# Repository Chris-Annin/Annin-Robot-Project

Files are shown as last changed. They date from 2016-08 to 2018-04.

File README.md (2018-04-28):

# Annin Robot Project

## 6 axis stepper motor robot and control software

This project includes:

- Bill of materials and instructions
- CAD files to 3D print components to build the robot
- Arduino sketch for stepper driver control
- Software to program and operate robot

All geared stepper motors and drivers are available from  [www.omc-stepperonline.com](https://www.omc-stepperonline.com/?tracking=59c1139e8987b)
all other misc hardware are off the shelf items available from multiple sources (see the bill of materials file)

(https://www.youtube.com/watch?v=XkAfb8alqnI)

This was my first Arduino program and my first python application using the Tk module.
I hope people will enjoy building thier own robot, utilize and improve the software
and design and build bigger and better robot units and share thier designs.

1. review the bill of materials
2. review the assembly instructions
3. download models and build robot
4. review calibration video [Calibration Video](https://youtu.be/jC1Iq60EnBI)
5. review programming video [Programming Video](https://youtu.be/hFJe0j0nB_w)

please view license file

Questions: chris.annin@gmail.com
#


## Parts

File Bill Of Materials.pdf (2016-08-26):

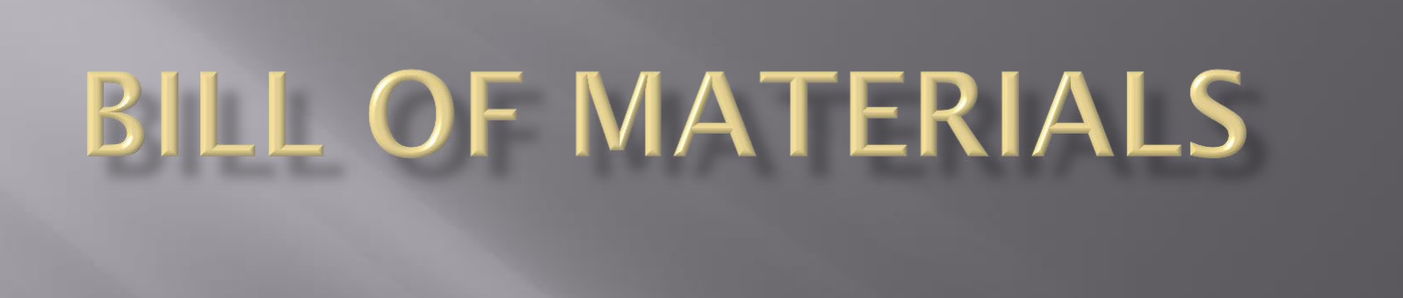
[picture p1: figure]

## This BOM includes all the major parts to build the robot. These parts were purchased from Amazon, McMaster Carr, Ebay, the local hardware store and also parts you need to print on your 3D

printer. There are a few misc. screws and wires I may have missed.

## If there is not a note below the picture stating quantity then just buy

one of the item shown.

# Amazon parts – these are in no particular order

You need a total of 3 of these bearings so I
Bought 2 (2 packs) | You need a total of 4 of these bearings

You need a total of 2 of these thrust bearings

I bought 2 of these 5vdc power supplies One to power the stepper drivers and one To power my relays

There is a cheaper power supply on Amazon that would probably work fine It needs to be 24vdc and 10 to 15 amp

You do not need the power supply – just the Breadboard and wires (power supply is garbage)

1 stepper motor for axis 5 1 stepper motor for axis 4

You need 2 of these needle bearings | 1 stepper motor for axis 6
For axis 4

You need 2 of these stepper motors for axis 1 and 2 1 stepper motors for axis 3

You need a total of 6 stepper drivers – so you Will need to purchase 2 (5 packs)

## This tubing was purchased From McMaster Carr

## This gear was from Ebay

## Parts purchased from local hardware store

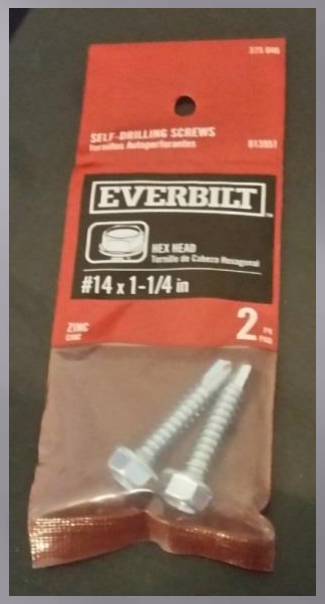
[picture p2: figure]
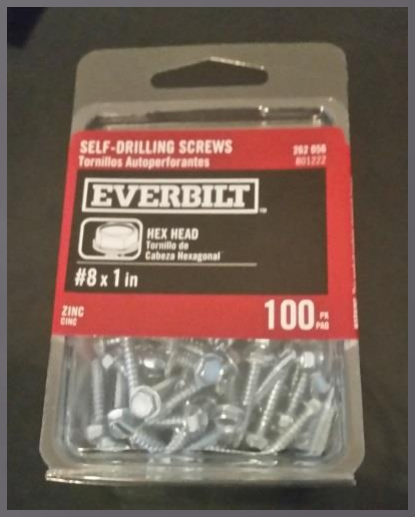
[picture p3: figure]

NEED 4 #14 SCREWS TO MOUNT BASE

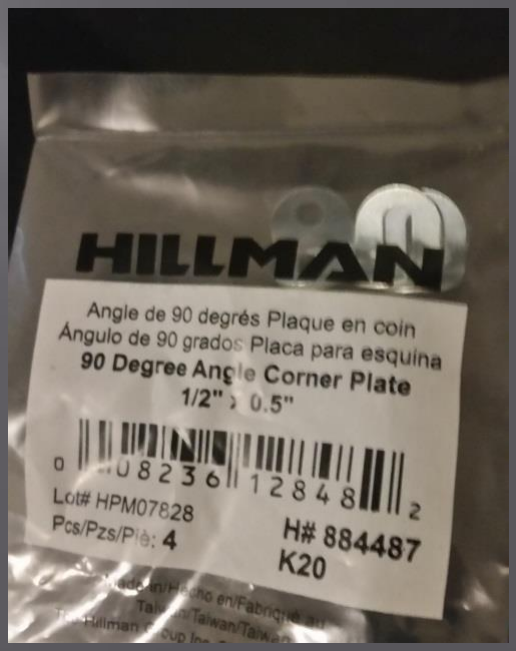
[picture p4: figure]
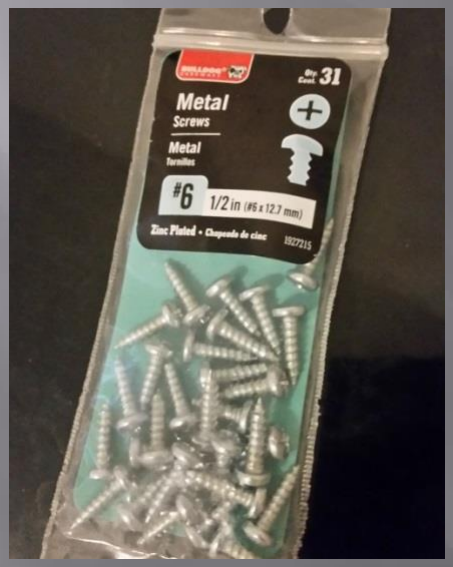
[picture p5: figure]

NEED #6 SCREW ½” AND 3/8” LONG

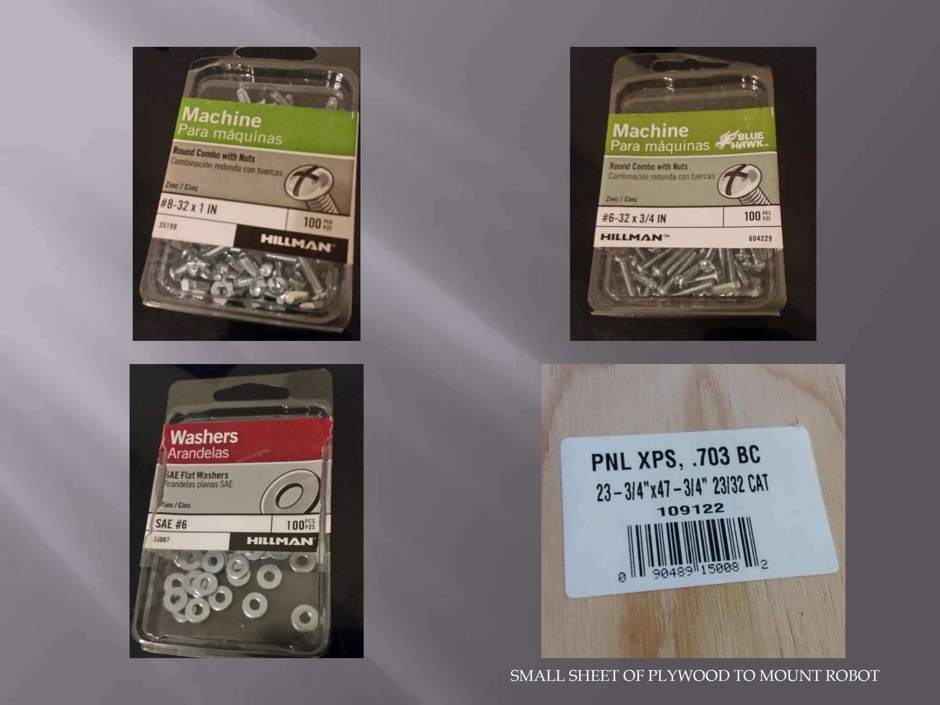
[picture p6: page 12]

SMALL SHEET OF PLYWOOD TO MOUNT ROBOT

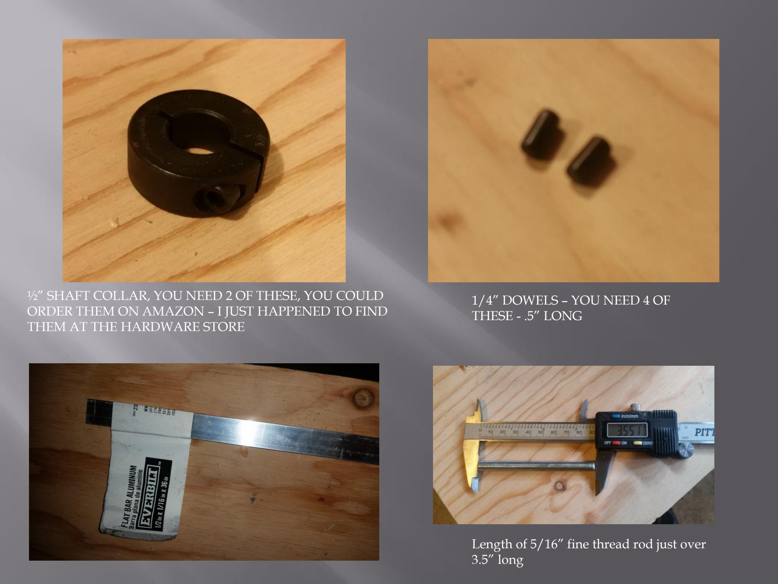
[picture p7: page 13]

½” SHAFT COLLAR, YOU NEED 2 OF THESE, YOU COULD ORDER THEM ON AMAZON – I JUST HAPPENED TO FIND THEM AT THE HARDWARE STORE

1/4” DOWELS – YOU NEED 4 OF THESE - .5” LONG

Length of 5/16” fine thread rod just over 3.5” long

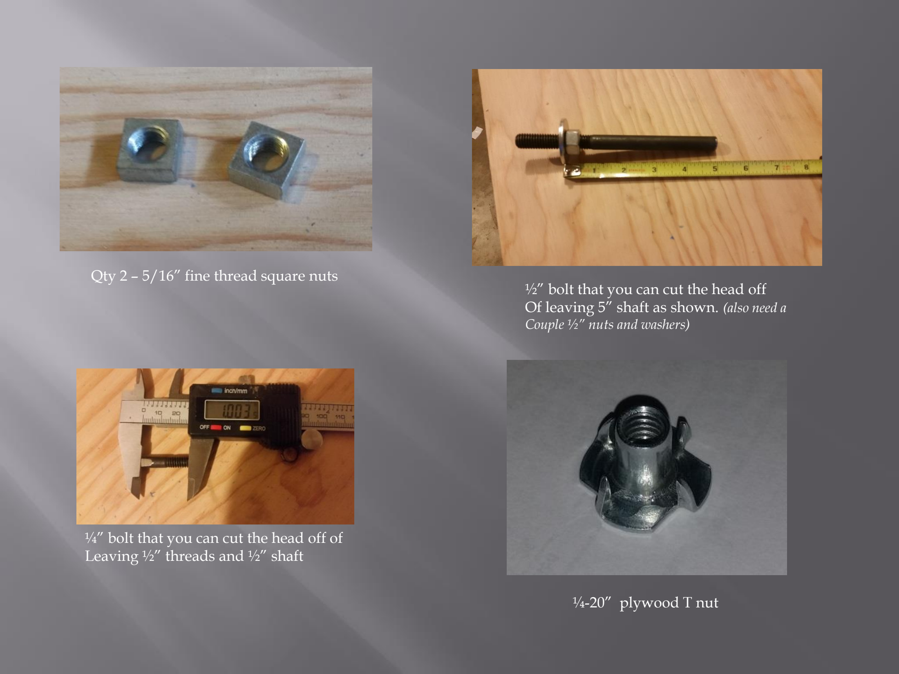
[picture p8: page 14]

Qty 2 – 5/16” fine thread square nuts ½” bolt that you can cut the head off Of leaving 5” shaft as shown. (also need a Couple ½” nuts and washers)

¼” bolt that you can cut the head off of Leaving ½” threads and ½” shaft

¼-20” plywood T nut

ADDITIONALLY YOU WILL NEED A NUMBER OF METRIC MACHINE SCREWS, 2mm & 3mm. I was able to find what I needed at the hardware store but you can also get screw assortments on Amazon.


¼-20” bolt that you can cut The head off leaving total 1” long With .5” threads and .5” shaft.


2” long coil springs – I got these out
Of a harbor freight spring assortment I had.

## Parts you need to print on your 3D printer

(I printed all these on a Davinci XYZ 1.0 - unless otherwise noted these were all printed at 50% solid, thick shells, 2mm layers, slow speed with no supports)

J1 Base | J1 Alignment Ring
J1 Turret | J1 Turret Cover

I didn’t have good luck using supports for these larger thin wall holes So I built the model with cut outs you will need to grind out with a dremel

J2 Arm Left
J2 Arm Right

J2 Spacers

J2 Motor Support

Used supports on this one

J2 Drive Rod Support Block J2 Drive Block

J2 Arm Cover (x2)
J3 Turret

Used supports on this one
Used supports on this one

Used supports on this one

J3 Spindle

Collar 1 inch

J3 Turret Cap | J4 Boom – Left & Right (left not pictured)
Used supports on this one | Used supports on this one

J5 Motor Mount

J5 Clevis Center | J5 Clevis Left Arm & Right Arm
J5 Turret Left and Right Arms / J5 Turret Center | Gear J5 Ring Carrier / Gear J5 Ring Carrier Cap Gear J5 Worm Bushing

Timing Belt Coupler
J4 Wire Holder (x2)

Gripper Motor Side Plate
Gripper Cover Side Plate Printed 90% solid on this one – wanted area where J6 motor

Shaft inserts to be solid

Gripper Center Spur Gear
Gripper Right Jaw
Gripper Left Jaw | Home Cradle

Printed 90% solid on this one Printed 90% solid on this one

Printed 90% solid on this one | Printed 30% solid on this one – this part doesn’t need much strength And is too large to print with much mass

Relay Board Mount

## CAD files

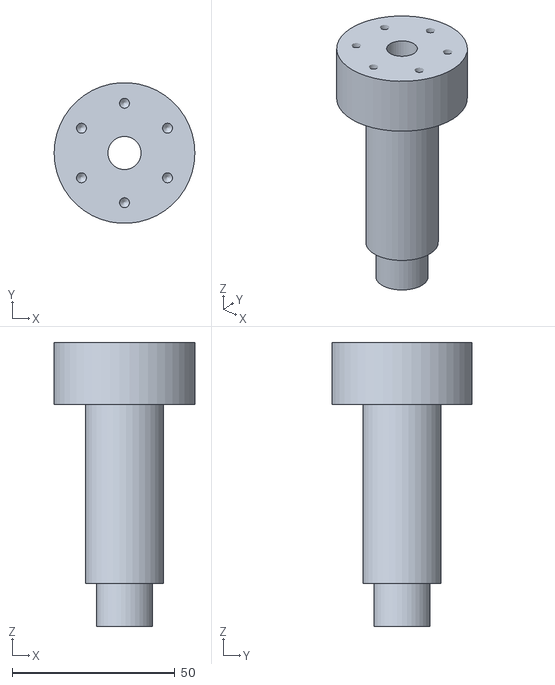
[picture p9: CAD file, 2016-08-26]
STL files/J3 Spindle.STL
43.2 x 43.1 x 87.1

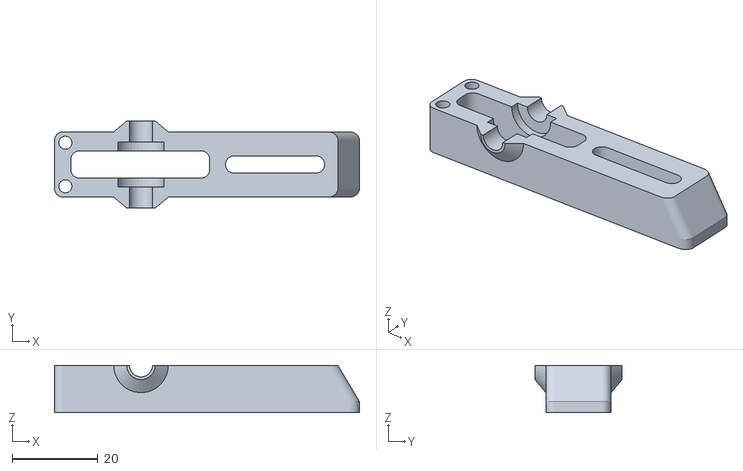
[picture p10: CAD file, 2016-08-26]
STL files/Gear J5 ring carrier.STL
71.1 x 20.3 x 11.0

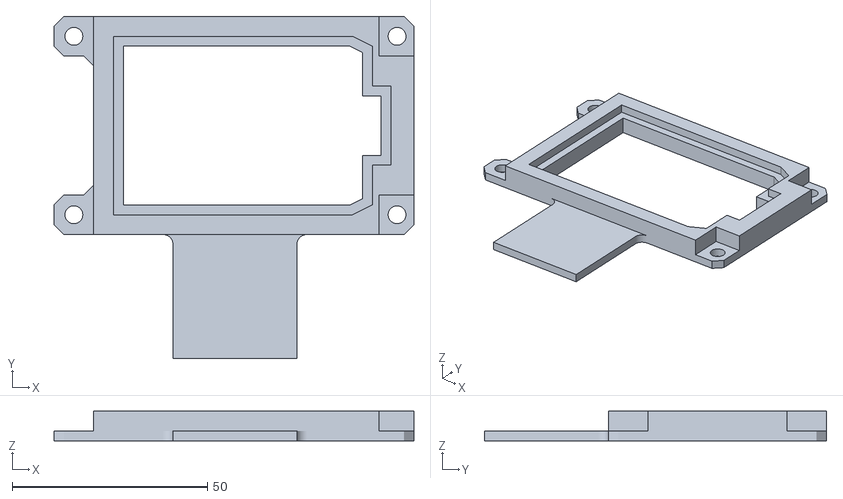
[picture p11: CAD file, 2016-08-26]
STL files/Mouse Holder.STL
92.2 x 87.6 x 7.62

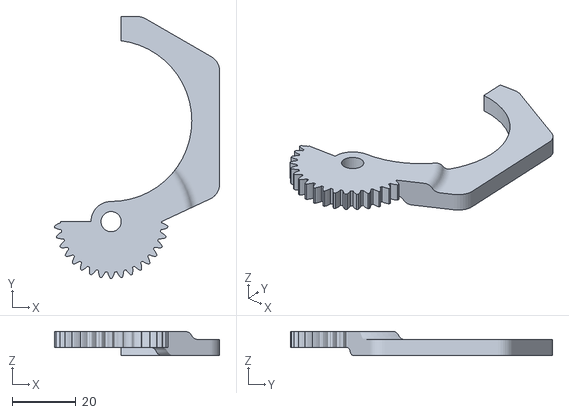
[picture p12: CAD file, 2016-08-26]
STL files/Gripper left jaw.STL
52.0 x 82.5 x 7.62

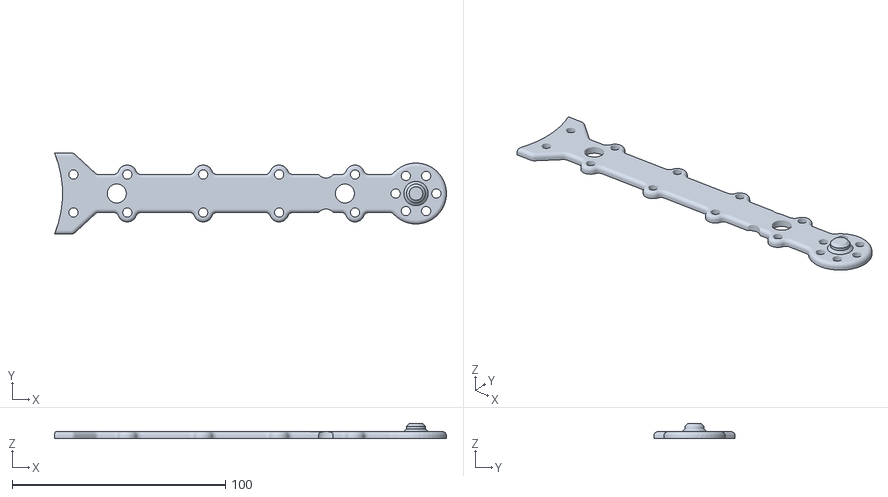
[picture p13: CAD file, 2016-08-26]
STL files/J2 Arm Cover.STL
183.6 x 38.0 x 6.98

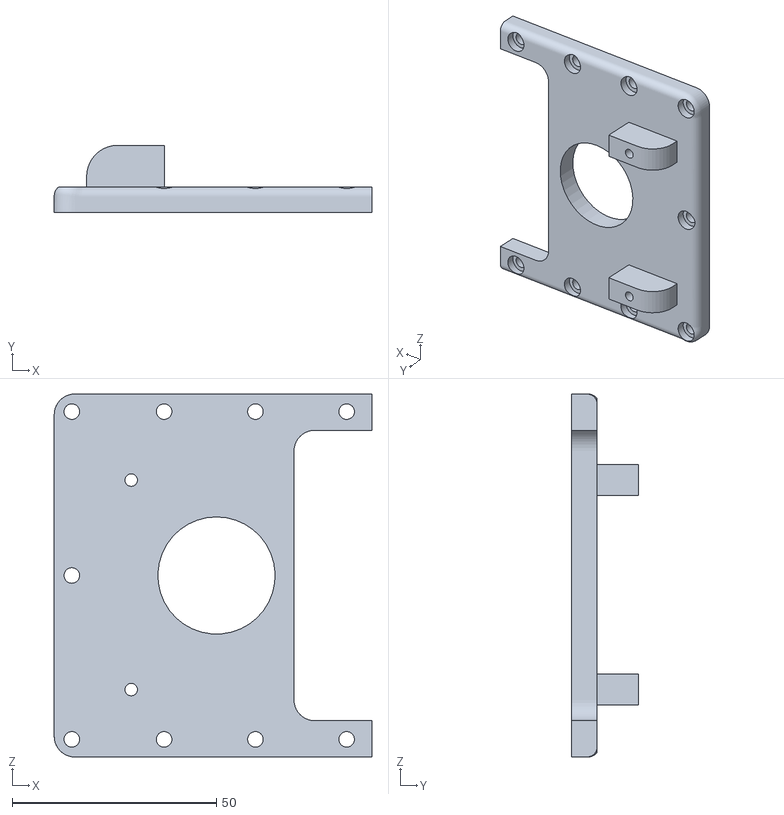
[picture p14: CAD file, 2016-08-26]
STL files/J1 Turret cover.STL
77.8 x 16.5 x 88.9

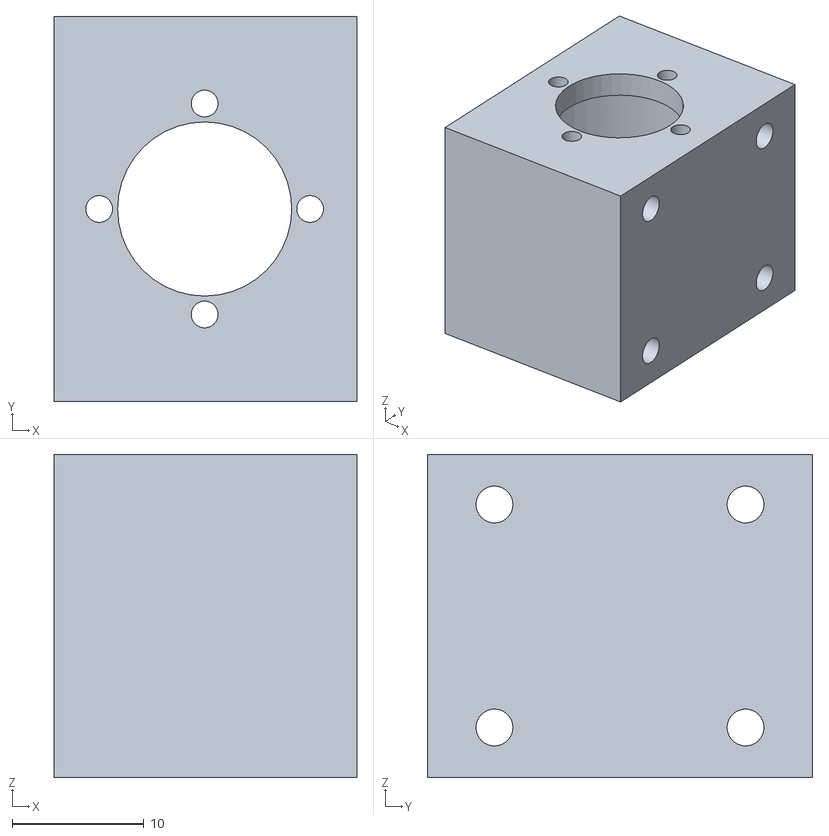
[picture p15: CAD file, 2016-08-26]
STL files/J5 Turret Center.STL
23.0 x 29.2 x 24.5

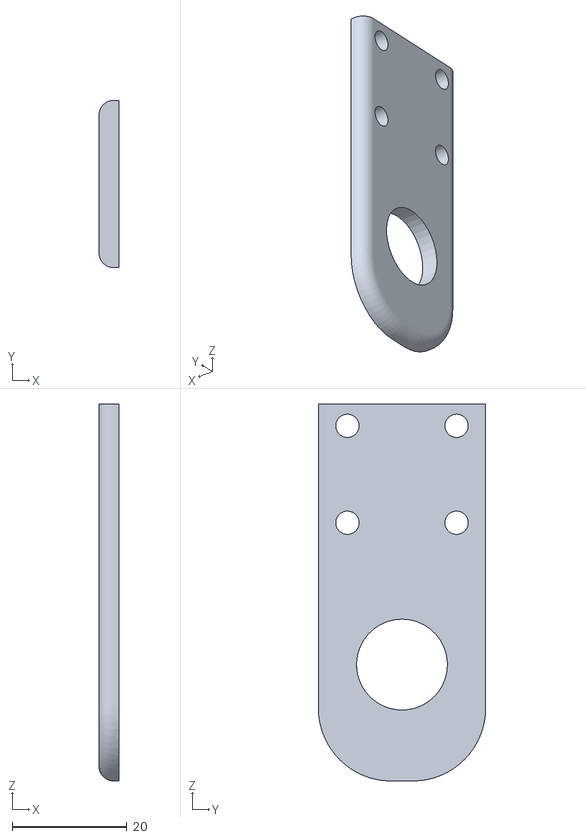
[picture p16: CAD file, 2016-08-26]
STL files/J5 Turret Right Arm.STL
3.49 x 29.2 x 65.8

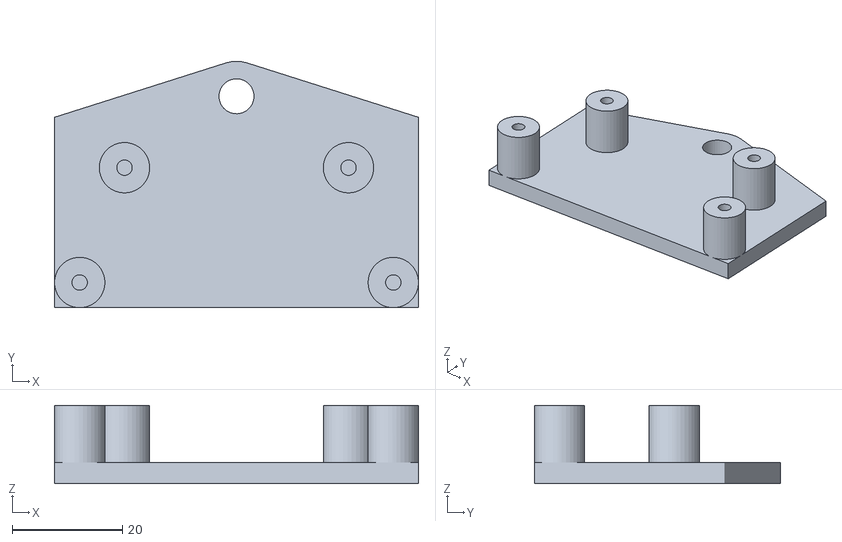
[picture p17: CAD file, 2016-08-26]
STL files/Gripper Cover side plate.STL
66.0 x 44.7 x 14.2

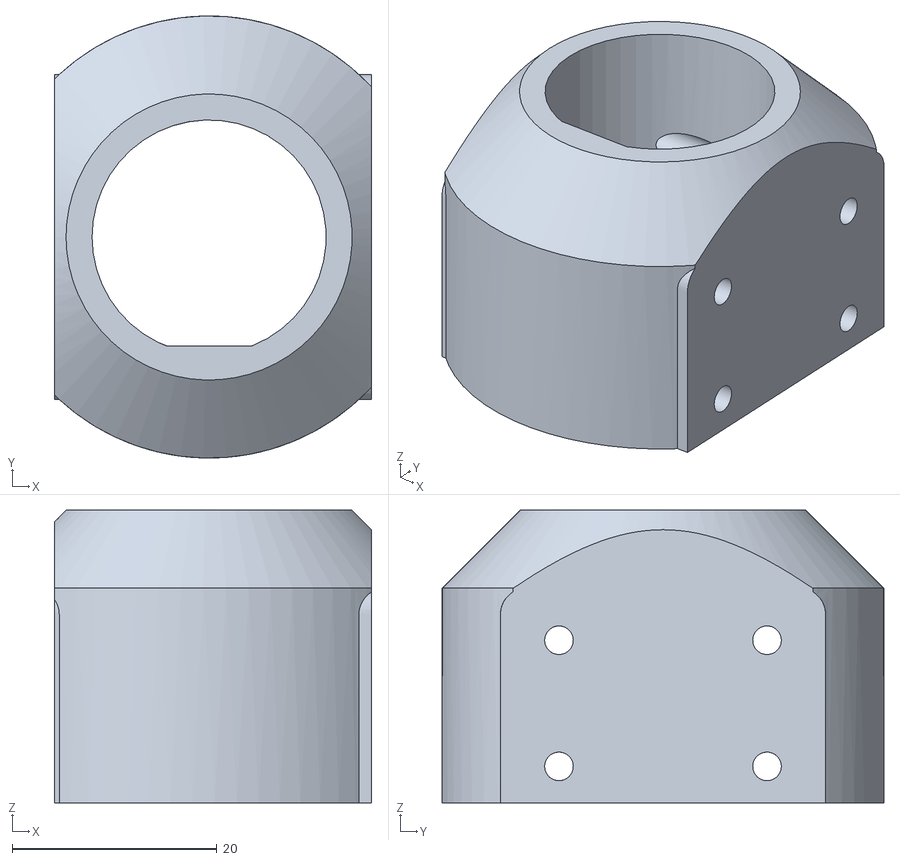
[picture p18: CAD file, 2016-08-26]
STL files/J5 Clevis Center.STL
31.0 x 43.2 x 28.6

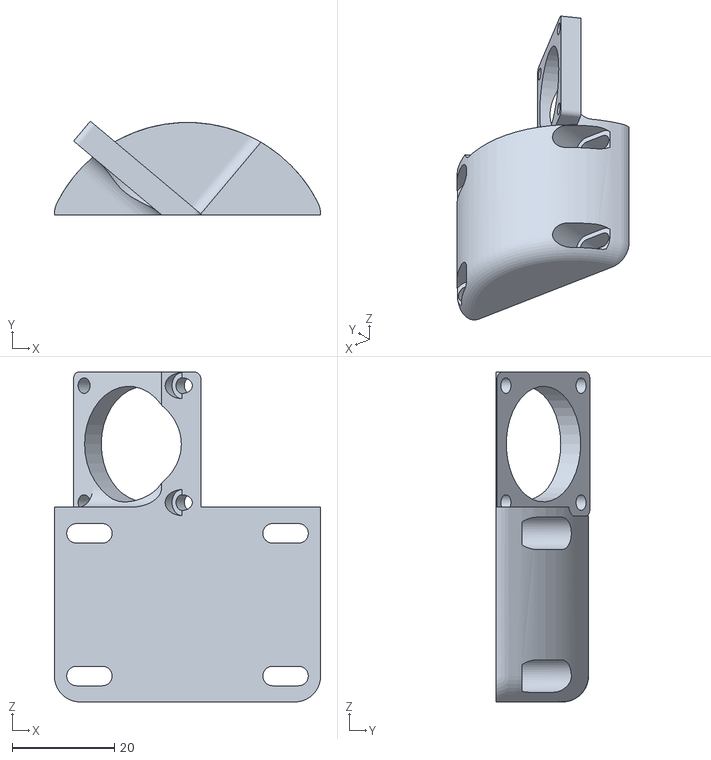
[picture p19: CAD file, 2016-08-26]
STL files/J3 Turret cap.STL
52.1 x 18.3 x 64.5

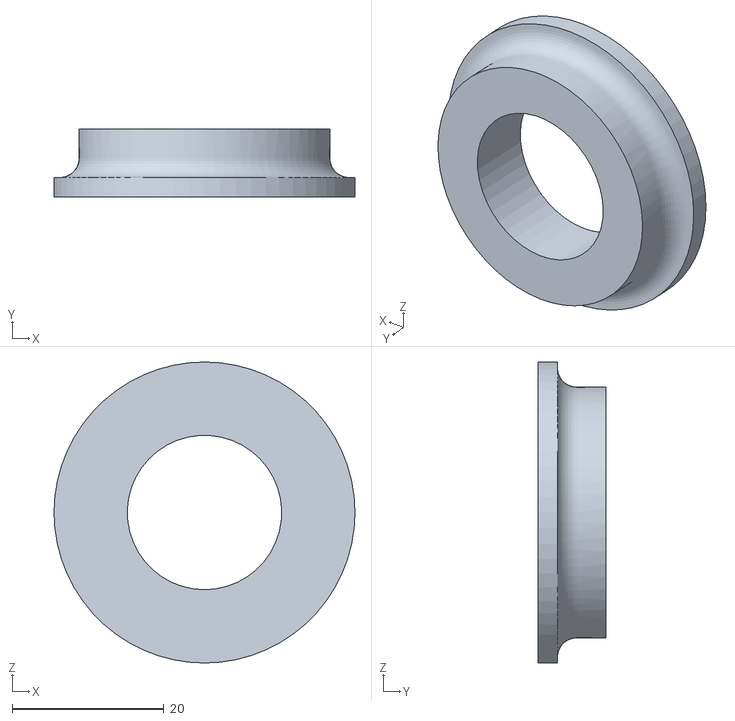
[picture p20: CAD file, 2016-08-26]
STL files/Collar 1 inch.STL
39.6 x 8.89 x 39.6

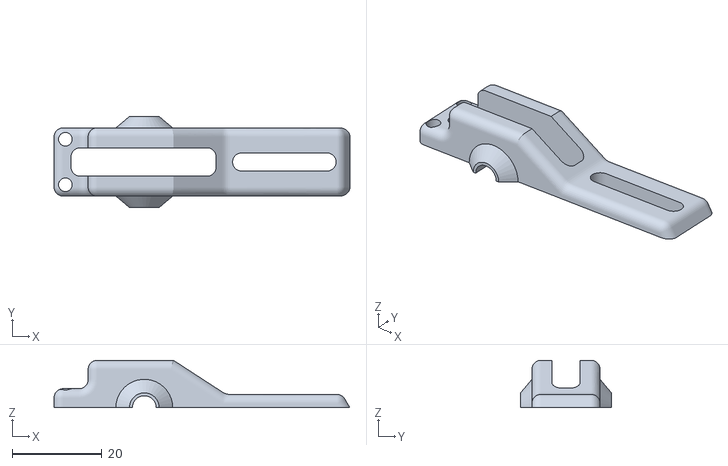
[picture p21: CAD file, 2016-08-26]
STL files/Gear J5 ring carrier cap.STL
66.1 x 20.3 x 10.6

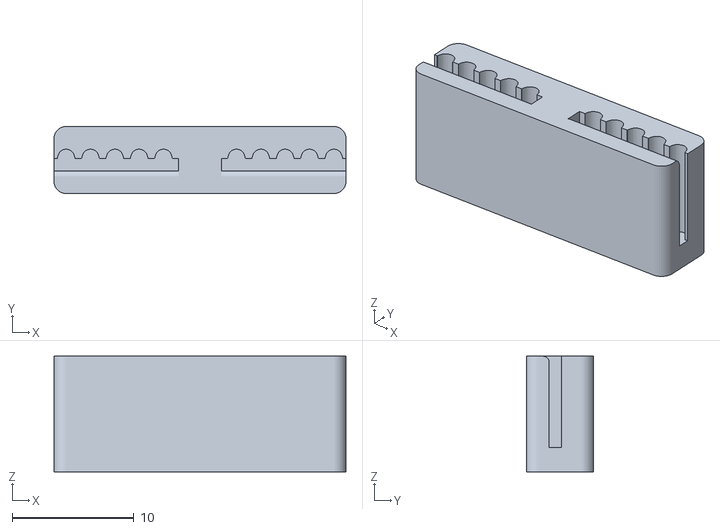
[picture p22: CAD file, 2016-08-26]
STL files/timing belt coupler.STL
24.0 x 5.52 x 9.50

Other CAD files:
STL files/Gripper right jaw.STL
STL files/J2 Spacer 2.STL
STL files/J2 Motor Support.STL
STL files/J2 Drive Rod Support Block.STL
STL files/Arduino Mount.STL
STL files/Gear J5 worm bushing.STL
STL files/Gripper Motor side plate.STL
STL files/Gripper center spur.STL
STL files/Home cradle.STL
STL files/J1 Alignment Ring.STL
STL files/J1 Base.STL
STL files/J1 Turret.STL
STL files/J2 Arm Left.STL
STL files/J2 Arm Right.STL
STL files/J2 Drive Block.STL
STL files/J2 Spacer.STL
STL files/J2 nut cap.STL
STL files/J3 Turret.STL
STL files/J4 Boom left.STL
STL files/J4 Boom right.STL
STL files/J4 Boom.STL
STL files/J4 Collar 1 inch.STL
STL files/J4 wire holder.STL
STL files/J5 Clevis Left Arm.STL
STL files/J5 Clevis Right Arm.STL
STL files/J5 Clevis.STL
STL files/J5 Motor Mount.STL
STL files/J5 Turret Left Arm.STL
STL files/J5 Turret.STL
STL files/coupler.STL

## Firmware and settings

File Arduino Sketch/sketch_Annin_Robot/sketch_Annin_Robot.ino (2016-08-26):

/* Annin Robot - Stepper motor robot control software
    Copyright (C) 2016  Chris Annin

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
    chris.annin@gmail.com
*/    

#include <Servo.h>

Servo servo0;
Servo servo1;
Servo servo2;
Servo servo3;
Servo servo4;
Servo servo5;
Servo servo6;
Servo servo7;

String inData;
String function;

const int J1stepPin = 2;
const int J1dirPin = 3;
const int J2stepPin = 4;
const int J2dirPin = 5;
const int J3stepPin = 6;
const int J3dirPin = 7;
const int J4stepPin = 8;
const int J4dirPin = 9;
const int J5stepPin = 10;
const int J5dirPin = 11;
const int J6stepPin = 12;
const int J6dirPin = 13;

const int Input22 = 22;
const int Input23 = 23;
const int Input24 = 24;
const int Input25 = 25;
const int Input26 = 26;
const int Input27 = 27;
const int Input28 = 28;
const int Input29 = 29;
const int Input30 = 30;
const int Input31 = 31;
const int Input32 = 32;
const int Input33 = 33;
const int Input34 = 34;
const int Input35 = 35;
const int Input36 = 36;
const int Input37 = 37;

const int Output38 = 38;
const int Output39 = 39;
const int Output40 = 40;
const int Output41 = 41;
const int Output42 = 42;
const int Output43 = 43;
const int Output44 = 44;
const int Output45 = 45;
const int Output46 = 46;
const int Output47 = 47;
const int Output48 = 48;
const int Output49 = 49;
const int Output50 = 50;
const int Output51 = 51;
const int Output52 = 52;
const int Output53 = 53;


void setup() {
  // put your setup code here, to run once:
  Serial.begin(9600);

  pinMode(A0, OUTPUT);
  pinMode(A1, OUTPUT);
  pinMode(A2, OUTPUT);
  pinMode(A3, OUTPUT);
  pinMode(A4, OUTPUT);
  pinMode(A5, OUTPUT);
  pinMode(A6, OUTPUT);
  pinMode(A7, OUTPUT);

  pinMode(J1stepPin, OUTPUT);
  pinMode(J1dirPin, OUTPUT);
  pinMode(J2stepPin, OUTPUT);
  pinMode(J2dirPin, OUTPUT);
  pinMode(J3stepPin, OUTPUT);
  pinMode(J3dirPin, OUTPUT);
  pinMode(J4stepPin, OUTPUT);
  pinMode(J4dirPin, OUTPUT);
  pinMode(J5stepPin, OUTPUT);
  pinMode(J5dirPin, OUTPUT);
  pinMode(J6stepPin, OUTPUT);
  pinMode(J6dirPin, OUTPUT);

  pinMode(Input22, INPUT);
  pinMode(Input23, INPUT);
  pinMode(Input24, INPUT);
  pinMode(Input25, INPUT);
  pinMode(Input26, INPUT);
  pinMode(Input27, INPUT);
  pinMode(Input28, INPUT);
  pinMode(Input29, INPUT);
  pinMode(Input30, INPUT);
  pinMode(Input31, INPUT);
  pinMode(Input32, INPUT);
  pinMode(Input33, INPUT);
  pinMode(Input34, INPUT);
  pinMode(Input35, INPUT);
  pinMode(Input36, INPUT);
  pinMode(Input37, INPUT);

  pinMode(Output38, OUTPUT);
  pinMode(Output39, OUTPUT);
  pinMode(Output40, OUTPUT);
  pinMode(Output41, OUTPUT);
  pinMode(Output42, OUTPUT);
  pinMode(Output43, OUTPUT);
  pinMode(Output44, OUTPUT);
  pinMode(Output45, OUTPUT);
  pinMode(Output46, OUTPUT);
  pinMode(Output47, OUTPUT);
  pinMode(Output48, OUTPUT);
  pinMode(Output49, OUTPUT);
  pinMode(Output50, OUTPUT);
  pinMode(Output51, OUTPUT);
  pinMode(Output52, OUTPUT);
  pinMode(Output53, OUTPUT);

  servo0.attach(A0);
  servo1.attach(A1);
  servo2.attach(A2);
  servo3.attach(A3);
  servo4.attach(A4);
  servo5.attach(A5);
  servo6.attach(A6);
  servo7.attach(A7);

  digitalWrite(Output38, HIGH);
  digitalWrite(Output39, HIGH);
  digitalWrite(Output40, HIGH);
  digitalWrite(Output41, HIGH);
  digitalWrite(Output42, HIGH);
  digitalWrite(Output43, HIGH);
  digitalWrite(Output44, HIGH);
  digitalWrite(Output45, HIGH);

}


void loop() {
  while (Serial.available() > 0)
  {
    char recieved = Serial.read();
    inData += recieved;
    // Process message when new line character is recieved
    if (recieved == '\n')
    {
      String function = inData.substring(0, 2);


      //-----COMMAND TO MOVE SERVO---------------------------------------------------
      //-----------------------------------------------------------------------
      if (function == "SV")
      {
        int SVstart = inData.indexOf('V');
        int POSstart = inData.indexOf('P');
        int servoNum = inData.substring(SVstart + 1, POSstart).toInt();
        int servoPOS = inData.substring(POSstart + 1).toInt();
        if (servoNum == 0)
        {
          servo0.write(servoPOS);
        }
        if (servoNum == 1)
        {
          servo1.write(servoPOS);
        }
        if (servoNum == 2)
        {
          servo2.write(servoPOS);
        }
        if (servoNum == 3)
        {
          servo3.write(servoPOS);
        }
        if (servoNum == 4)
        {
          servo4.write(servoPOS);
        }
        if (servoNum == 5)
        {
          servo5.write(servoPOS);
        }
        if (servoNum == 6)
        {
          servo6.write(servoPOS);
        }
        if (servoNum == 7)
        {
          servo7.write(servoPOS);
        }
        Serial.print("Servo Done");
      }




      //-----COMMAND TO WAIT TIME---------------------------------------------------
      //-----------------------------------------------------------------------
      if (function == "WT")
      {
        int WTstart = inData.indexOf('S');
        float WaitTime = inData.substring(WTstart + 1).toFloat();
        int WaitTimeMS = WaitTime * 1000;
        delay(WaitTimeMS);
        Serial.print("Done");
      }

      //-----COMMAND IF INPUT THEN JUMP---------------------------------------------------
      //-----------------------------------------------------------------------
      if (function == "IJ")
      {
        int IJstart = inData.indexOf('X');
        int IJTabstart = inData.indexOf('T');
        int IJInputNum = inData.substring(IJstart + 1, IJTabstart).toInt();
        if (digitalRead(IJInputNum) == HIGH)
        {
          Serial.println("True\n");
        }
        if (digitalRead(IJInputNum) == LOW)
        {
          Serial.println("False\n");
        }
      }
      //-----COMMAND SET OUTPUT ON---------------------------------------------------
      //-----------------------------------------------------------------------
      if (function == "ON")
      {
        int ONstart = inData.indexOf('X');
        int outputNum = inData.substring(ONstart + 1).toInt();
        digitalWrite(outputNum, HIGH);
        Serial.print("Done");
      }
      //-----COMMAND SET OUTPUT OFF---------------------------------------------------
      //-----------------------------------------------------------------------
      if (function == "OF")
      {
        int ONstart = inData.indexOf('X');
        int outputNum = inData.substring(ONstart + 1).toInt();
        digitalWrite(outputNum, LOW);
        Serial.print("Done");
      }
      //-----COMMAND TO WAIT INPUT ON---------------------------------------------------
      //-----------------------------------------------------------------------
      if (function == "WI")
      {
        int WIstart = inData.indexOf('N');
        int InputNum = inData.substring(WIstart + 1).toInt();
        while (digitalRead(InputNum) == LOW) {
          delay(100);
        }
        Serial.print("Done");
      }
      //-----COMMAND TO WAIT INPUT OFF---------------------------------------------------
      //-----------------------------------------------------------------------
      if (function == "WO")
      {
        int WIstart = inData.indexOf('N');
        int InputNum = inData.substring(WIstart + 1).toInt();

        //String InputStr =  String("Input" + InputNum);
        //uint8_t Input = atoi(InputStr.c_str ());
        while (digitalRead(InputNum) == HIGH) {
          delay(100);
        }
        Serial.print("Done");
      }
      //-----COMMAND TO MOVE---------------------------------------------------
      //-----------------------------------------------------------------------
      if (function == "MJ")
      {
        int J1start = inData.indexOf('A');
        int J2start = inData.indexOf('B');
        int J3start = inData.indexOf('C');
        int J4start = inData.indexOf('D');
        int J5start = inData.indexOf('E');
        int J6start = inData.indexOf('F');
        int SPstart = inData.indexOf('S');
        int J1dir = inData.substring(J1start + 1, J1start + 2).toInt();
        int J2dir = inData.substring(J2start + 1, J2start + 2).toInt();
        int J3dir = inData.substring(J3start + 1, J3start + 2).toInt();
        int J4dir = inData.substring(J4start + 1, J4start + 2).toInt();
        int J5dir = inData.substring(J5start + 1, J5start + 2).toInt();
        int J6dir = inData.substring(J6start + 1, J6start + 2).toInt();
        int J1step = inData.substring(J1start + 2, J2start).toInt();
        int J2step = inData.substring(J2start + 2, J3start).toInt();
        int J3step = inData.substring(J3start + 2, J4start).toInt();
        int J4step = inData.substring(J4start + 2, J5start).toInt();
        int J5step = inData.substring(J5start + 2, J6start).toInt();
        int J6step = inData.substring(J6start + 2, SPstart).toInt();
        float SpeedIn = inData.substring(SPstart + 1).toFloat();
        SpeedIn = (SpeedIn / 100);
        float CalcSpeed = (1600 / SpeedIn);
        int Speed = int(CalcSpeed);

        //FIND HIGHEST STEP
        int highStep = J1step;
        if (J2step > highStep)
        {
          highStep = J2step;
        }
        if (J3step > highStep)
        {
          highStep = J3step;
        }
        if (J4step > highStep)
        {
          highStep = J4step;
        }
        if (J5step > highStep)
        {
          highStep = J5step;
        }
        if (J6step > highStep)
        {
          highStep = J6step;
        }



        //DETERMINE AXIS SKIP INCREMENT
        int J1skip = (highStep / J1step);
        int J2skip = (highStep / J2step);
        int J3skip = (highStep / J3step);
        int J4skip = (highStep / J4step);
        int J5skip = (highStep / J5step);
        int J6skip = (highStep / J6step);


        //RESET COUNTERS
        int J1done = 0;
        int J2done = 0;
        int J3done = 0;
        int J4done = 0;
        int J5done = 0;
        int J6done = 0;

        //RESET SKIP CURRENT
        int J1skipCur = 0;
        int J2skipCur = 0;
        int J3skipCur = 0;
        int J4skipCur = 0;
        int J5skipCur = 0;
        int J6skipCur = 0;

        //SET DIRECTIONS
        if (J1dir == 1)
        {
          digitalWrite(J1dirPin, HIGH);
        }
        else if (J1dir == 0)
        {
          digitalWrite(J1dirPin, LOW);
        }
        if (J2dir == 1)
        {
          digitalWrite(J2dirPin, HIGH);
        }
        else if (J2dir == 0)
        {
          digitalWrite(J2dirPin, LOW);
        }
        if (J3dir == 1)
        {
          digitalWrite(J3dirPin, HIGH);
        }
        else if (J3dir == 0)
        {
          digitalWrite(J3dirPin, LOW);
        }
        if (J4dir == 1)
        {
          digitalWrite(J4dirPin, HIGH);
        }
        else if (J4dir == 0)
        {
          digitalWrite(J4dirPin, LOW);
        }
        if (J5dir == 1)
        {
          digitalWrite(J5dirPin, HIGH);
        }
        else if (J5dir == 0)
        {
          digitalWrite(J5dirPin, LOW);
        }
        if (J6dir == 1)
        {
          digitalWrite(J6dirPin, HIGH);
        }
        else if (J6dir == 0)
        {
          digitalWrite(J6dirPin, LOW);
        }




        //DRIVE MOTORS
        while (J1done < J1step || J2done < J2step || J3done < J3step || J4done < J4step || J5done < J5step || J6done < J6step)
        {
          if (J1done < J1step && J1skipCur == 0)
          {
            digitalWrite(J1stepPin, HIGH);
          }
          if (J2done < J2step && J2skipCur == 0)
          {
            digitalWrite(J2stepPin, HIGH);
          }
          if (J3done < J3step && J3skipCur == 0)
          {
            digitalWrite(J3stepPin, HIGH);
          }
          if (J4done < J4step && J4skipCur == 0)
          {
            digitalWrite(J4stepPin, HIGH);
          }
          if (J5done < J5step && J5skipCur == 0)
          {
            digitalWrite(J5stepPin, HIGH);
          }
          if (J6done < J6step && J6skipCur == 0)
          {
            digitalWrite(J6stepPin, HIGH);
          }
          //#############DELAY AND SET LOW
          delayMicroseconds(0);
          if (J1done < J1step && J1skipCur == 0)
          {
            digitalWrite(J1stepPin, LOW);
            J1done = ++J1done;
          }
          if (J2done < J2step && J2skipCur == 0)
          {
            digitalWrite(J2stepPin, LOW);
            J2done = ++J2done;
          }
          if (J3done < J3step && J3skipCur == 0)
          {
            digitalWrite(J3stepPin, LOW);
            J3done = ++J3done;
          }
          if (J4done < J4step && J4skipCur == 0)
          {
            digitalWrite(J4stepPin, LOW);
            J4done = ++J4done;
          }
          if (J5done < J5step && J5skipCur == 0)
          {
            digitalWrite(J5stepPin, LOW);
            J5done = ++J5done;;
          }
          if (J6done < J6step && J6skipCur == 0)
          {
            digitalWrite(J6stepPin, LOW);
            J6done = ++J6done;
          }
          //#############DELAY BEFORE RESTARTING LOOP AND SETTING HIGH AGAIN
          delayMicroseconds(Speed);
          //increment skip count
          J1skipCur = ++J1skipCur;
          J2skipCur = ++J2skipCur;
          J3skipCur = ++J3skipCur;
          J4skipCur = ++J4skipCur;
          J5skipCur = ++J5skipCur;
          J6skipCur = ++J6skipCur;
          //if skiped enough times set back to zero
          if (J1skipCur == J1skip)
          {
            J1skipCur = 0;
          }
          if (J2skipCur == J2skip)
          {
            J2skipCur = 0;
          }
          if (J3skipCur == J3skip)
          {
            J3skipCur = 0;
          }
          if (J4skipCur == J4skip)
          {
            J4skipCur = 0;
          }
          if (J5skipCur == J5skip)
          {
            J5skipCur = 0;
          }
          if (J6skipCur == J6skip)
          {
            J6skipCur = 0;
          }
        }
        inData = ""; // Clear recieved buffer
        Serial.print("Move Done");
      }
      else
      {
        inData = ""; // Clear recieved buffer
      }
    }
  }
}

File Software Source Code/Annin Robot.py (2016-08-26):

##########################################################################
##########################################################################
""" Annin Robot - Stepper motor robot control software
    Copyright (C) 2016  Chris Annin

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
    chris.annin@gmail.com
"""
##########################################################################
##########################################################################


from Tkinter import *
import pickle
import serial
import time
import threading
import Queue

root = Tk()
root.wm_title("Annin Robot 1.0")
root.iconbitmap(r'ARbot.ico')
root.resizable(width=True, height=True)
root.geometry('{}x{}'.format(1024,700))
root.runTrue = 0


###DEFS###################################################################
##########################################################################


def setCom():
  global ser  
  port = "COM" + comPortEntryField.get()  
  baud = 9600 
  ser = serial.Serial(port, baud)

def deleteitem():
  selRow = root.progView.curselection()[0]
  selection = root.progView.curselection()  
  root.progView.delete(selection[0])
  root.progView.select_set(selRow)  
  value=root.progView.get(0,END)
  pickle.dump(value,open(ProgEntryField.get(),"wb"))
    

def executeRow():
  selRow = root.progView.curselection()[0]
  root.progView.see(selRow+2)
  data = map(int, root.progView.curselection())
  command=root.progView.get(data[0])
  cmdType=command[:6]
  ##Call Program##
  if (cmdType == "Call P"):
    root.lastRow = root.progView.curselection()[0]
    root.lastProg = ProgEntryField.get()
    programIndex = command.find("Program -")
    progNum = str(command[programIndex+10:])
    ProgEntryField.delete(0, 'end')
    ProgEntryField.insert(0,progNum)
    loadProg()
    time.sleep(.2)    
    index = 0
    root.progView.selection_clear(0, END)
    root.progView.select_set(index) 
  ##Return Program##
  if (cmdType == "Return"):
    lastRow = root.lastRow
    lastProg = root.lastProg
    ProgEntryField.delete(0, 'end')
    ProgEntryField.insert(0,lastProg)
    loadProg()
    time.sleep(.2)    
    index = 0
    root.progView.selection_clear(0, END)
    root.progView.select_set(lastRow)  
  ##Servo Command##
  if (cmdType == "Servo "):
    servoIndex = command.find("number ")
    posIndex = command.find("position: ")
    servoNum = str(command[servoIndex+7:posIndex-4])
    servoPos = str(command[posIndex+10:])
    command = "SV"+servoNum+"P"+servoPos
    ser.write(command +"\n")
    ser.flushInput()
    time.sleep(.1)  
    ser.read() 
  ##If Input On Jump to Tab##
  if (cmdType == "If On "):
    inputIndex = command.find("Input-")
    tabIndex = command.find("Tab-")
    inputNum = str(command[inputIndex+6:tabIndex-9])
    tabNum = str(command[tabIndex+4:])
    command = "JFX"+inputNum+"T"+tabNum   
    ser.write(command +"\n")
    ser.flushInput()
    value = ser.readline()
    #value = str(value[3:])
    manEntryField.delete(0, 'end')
    manEntryField.insert(0,value)
    if (value == "True\n"):
      index = root.progView.get(0, "end").index("Tab Number " + tabNum)
      index = index-1
      root.progView.selection_clear(0, END)
      root.progView.select_set(index)
  ##If Input Off Jump to Tab##
  if (cmdType == "If Off"):
    inputIndex = command.find("Input-")
    tabIndex = command.find("Tab-")
    inputNum = str(command[inputIndex+6:tabIndex-9])
    tabNum = str(command[tabIndex+4:])
    command = "JFX"+inputNum+"T"+tabNum   
    ser.write(command +"\n")
    ser.flushInput()
    value = ser.readline()
    #value = str(value[3:])
    manEntryField.delete(0, 'end')
    manEntryField.insert(0,value)
    if (value == "False\n"):
      index = root.progView.get(0, "end").index("Tab Number " + tabNum)
      index = index-1
      root.progView.selection_clear(0, END)
      root.progView.select_set(index)
  ##Jump to Row##
  if (cmdType == "Jump T"):
    tabIndex = command.find("Tab-")
    tabNum = str(command[tabIndex+4:])
    index = root.progView.get(0, "end").index("Tab Number " + tabNum)
    root.progView.selection_clear(0, END)
    root.progView.select_set(index)  
  ##Set Output ON Command##
  if (cmdType == "Out On"):
    outputIndex = command.find("Output-")
    outputNum = str(command[outputIndex+7:])
    command = "ONX"+outputNum
    ser.write(command +"\n")
    ser.flushInput()
    time.sleep(.1)  
    ser.read() 
  ##Set Output OFF Command##
  if (cmdType == "Out Of"):
    outputIndex = command.find("Output-")
    outputNum = str(command[outputIndex+7:])
    command = "OFX"+outputNum
    ser.write(command +"\n")
    ser.flushInput()
    time.sleep(.1)  
    ser.read() 
  ##Wait Input ON Command##
  if (cmdType == "Wait I"):
    inputIndex = command.find("Input-")
    inputNum = str(command[inputIndex+6:])
    command = "WIN"+inputNum
    ser.write(command +"\n")
    ser.flushInput()
    time.sleep(.1)  
    ser.read() 
  ##Wait Input OFF Command##
  if (cmdType == "Wait O"):
    inputIndex = command.find("Input-")
    inputNum = str(command[inputIndex+6:])
    command = "WON"+inputNum
    ser.write(command +"\n")
    ser.flushInput()
    time.sleep(.1)  
    ser.read() 
  ##Wait Time Command##
  if (cmdType == "Wait T"):
    timeIndex = command.find("Seconds-")
    timeSeconds = str(command[timeIndex+8:])
    command = "WTS"+timeSeconds
    ser.write(command +"\n")
    ser.flushInput()
    time.sleep(.1)  
    ser.read() 
  ##Move Command##  
  if (cmdType == "Move J"):  
    J1curAng = J1curAngEntryField.get()
    J2curAng = J2curAngEntryField.get()
    J3curAng = J3curAngEntryField.get()
    J4curAng = J4curAngEntryField.get()
    J5curAng = J5curAngEntryField.get()
    J6curAng = J6curAngEntryField.get()
    J1newIndex = command.find("J1-")
    J2newIndex = command.find("J2-")
    J3newIndex = command.find("J3-")
    J4newIndex = command.find("J4-")
    J5newIndex = command.find("J5-")
    J6newIndex = command.find("J6-")
    SpeedIndex = command.find("Speed-")
    J1newAng = command[J1newIndex+3:J2newIndex-1]
    J2newAng = command[J2newIndex+3:J3newIndex-1]
    J3newAng = command[J3newIndex+3:J4newIndex-1]
    J4newAng = command[J4newIndex+3:J5newIndex-1]
    J5newAng = command[J5newIndex+3:J6newIndex-1]
    J6newAng = command[J6newIndex+3:SpeedIndex-1]
    newSpeed = str(command[SpeedIndex+6:])
    ##J1 calc##
    J1degStep = float(J1degPerStepEntryField.get())
    J1curStep = int(J1curStepEntryField.get())
    if (float(J1newAng) >= float(J1curAng)):
      ####SET DIRECTION
      J1dir = "1"
      J1calcAng = float(J1newAng) - float(J1curAng)
      J1steps = int(J1calcAng / J1degStep)
      J1newSteps = J1curStep + J1steps
      J1curStepEntryField.delete(0, 'end')
      J1curStepEntryField.insert(0,str(J1newSteps))       
      J1writeAng = float(J1curAng) + J1calcAng
      J1curAngEntryField.delete(0, 'end')
      J1curAngEntryField.insert(0,str(J1writeAng))    
      J1steps = str(J1steps) 
    elif(float(J1newAng) < float(J1curAng)): 
      J1dir = "0"
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

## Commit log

2016-08-26 Add BOM & Assembly instructions
2016-08-26 STL files
    [Arduino Mount.STL, Collar 1 inch.STL, Gear J5 ring carrier cap.STL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]
2016-08-26 Add software and arduino sketch
    [Collar 1 inch.STEP, Gear J5 ring carrier cap.STEP, Gear J5 ring carrier.STEP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]
2016-08-26 remove individual step files add zip
    [Collar 1 inch.STEP, Gear J5 ring carrier cap.STEP, Gear J5 ring carrier.STEP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]

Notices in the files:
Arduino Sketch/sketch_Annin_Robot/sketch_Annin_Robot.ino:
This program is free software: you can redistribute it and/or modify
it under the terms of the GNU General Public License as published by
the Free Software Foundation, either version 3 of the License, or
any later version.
